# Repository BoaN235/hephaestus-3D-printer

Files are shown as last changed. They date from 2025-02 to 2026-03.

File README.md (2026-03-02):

# Hephaestus-1v2
title: "Hephaestus-1v2"
description: "A Core XY Printer with a z axis tilt"
Made by : Boa_N

Total Time: 7 hours

## Goals and Requirments
- Idk if i wanna do 235x235 or 220x220
- CoreXY
- Encolsed
- Z Tilt bed
- Compressed into a small footprint ~360x360x470 mm or ~14.17x14.17x18.5 in
- I would like to design a pcb for this project

## info
  This version was built with the old parts of Hephaestus-1 an broken Ender 3V3 and a few new parts

## log
- ### Feb 21st - Feb 24th Toolhead Work Time: 2.5 hours
  
  

- ### Feb 25th - Mar 1st Main Body Overall Design Time 3.5 hours
  

# ------------------| OLD VERSION |------------------

# Hephaestus-1
title: "Hephaestus-1"
description: "A Core XY Printer"
Made by : Boa_N

Total time: 145 hours 50 mins (Idk how accurate this is probably pretty close tho)

- [x] I have a 3D printer or will be getting one before March 21st (friend)
  
Hephaestus is the god of artisens and craftsman. with this printer I want to be able to create cool things just like a artisen or craftsman would.

Nicknamed "fire hazard"

hpdrawingpng

## Goals and Requirments
- standard 235 x 235mm
- CoreXY
- Enclosed
- at least 150mm/s
- Klipper
- Open-Source
- won't burn my house down (I hope)
- Rigid for good printing qualtiy
- A Cool Logo Embossed somewhere
- RGB lights

## Helpfull Resources
- www.matterhackers.com/articles/anatomy-of-a-3d-printer

## BOM (Bill Of Materials)
| Name | Price | Amount | Total Price | Link | Quanity | Notes |
|---|---|---|---|---|---|---|
| Sherpa Extruder | 36.89 | 1 | 36.89 | [link](https://www.amazon.com/Accessories-Lightweight-Extruder-Compatible-Ender3v2/dp/B0CNPG9QB2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) | 1 | |
| E3D V6 | 13.5  | 1 | 13.5 | [link](https://www.amazon.com/Wangdd22-1-75mm-Printer-Extruder-Accessories/dp/B06XBXDJY3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) | 1 | |
| mini fan 2-pack | 10.99 | 1 | 10.99 | [link](https://www.amazon.com/MakerFocus-Printer-40X40X10mm-Appliances-Replacement/dp/B07CH6YC32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) | 2 | |
| linear rail guide 2pc | 35.99 | 1 | 35.99 | [link](https://www.amazon.com/IMETRX-MGN12H-Printer-Machine-Upgrade/dp/B09ZPHPB5F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) | 2 | |
| Timing Belt 5M & pullys | 16.99 | 1 | 16.99 | [link](https://www.amazon.com/Zeelo-Timing-Tensioner-Torsion-Printer/dp/B08SMFM3Z6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) | 7 | |
| Al Exstrusion 2020 400mm 8pc | 26.99 | 1 | 26.99 | [link](https://www.amazon.com/Aluminum-Extrusion-European-Standard-Anodized/dp/B0CLGZ614N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) | 8 | |
| SKR Mini BigTree V3 | 39.99 | 1 | 39.99 | [link](https://www.microcenter.com/product/645749/bigtreetech-upgrade-skr-mini-e3-v30-control-board-32bit-for-ender-3-motherboard-silent-board-with-tmc2209-uart-stepper-dri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) | 1 | |
| Nema Stepper Moter 3PC | 16.1  | 1 | 16.1 | [link](https://www.amazon.com/BESJMYT-Stepper-39-65oz-1-3A-2-86V-1-66x1-66x1-5inch/dp/B0D22DR6P5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) | 3 | |
| Hot Bed | 18.59 | 1 | 18.59 | [link](https://www.amazon.com/Aluminum-Heated-Upgrade-Printer-220x220mm/dp/B09QWBSD3B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) | 1 | |
| BedScrews | 11.69 | 1 | 11.69 | [link](https://www.amazon.com/TIOPY-Printer-Leveling-Upgrade-Silicone/dp/B0BRCXX769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) | 0 | |
| EndStops | 8.99  | 1 | 8.99 | [link](https://www.amazon.com/ALMOCN-Mechanical-Endstop-Switch-Printer/dp/B08L5W4WM5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) | 6 | |
| Lead Screw | 9.99  | 1 | 9.99 | [link](https://www.amazon.com/ReliaBot-400mm-Thread-Starts-Printer/dp/B078R2XLXW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) | 1 | |
| Power Supply | 20.66 | 1 | 20.66 | [link](https://www.amazon.com/SUPERNIGHT-Switching-Universal-Regulated-Transformer/dp/B01LATMSGS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) | 1 | |
| Rasbery Pi | 24.99 | 0 | 0 | [link](https://www.microcenter.com/product/514076/raspberry-pi-3-model-a-board) | 1 | |
| PTFE Tubes | 8.99  | 1 | 8.99 | [link](https://www.amazon.com/Ultra-Smooth-Teflon-Tubing-Friction-Creality/dp/B0DLV5C1JS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) | 1 | |
| 1 Stepper moter | 6.99  | 1 | 6.99 | [link](https://www.amazon.com/Nema17-Stepper-Motor-Bipolar-4-Lead/dp/B09SV33XS2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) | 1 | |
| M3-Screws | 9.99  | 1 | 9.99 | [link](https://www.amazon.com/800Pcs-Socket-Assortment-Washers-Printing/dp/B0DR92YVL5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) | 800 | |
| M5-Screws | 9.99  | 1 | 9.99 | [link](https://www.amazon.com/Bemaka-200PCS-Button-Washers-Assortment/dp/B0CSY7FMQD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) | 200 | |
| M3-M5 heated Inserts | 15.98 | 1 | 15.98 | [link](https://www.amazon.com/Ktehloy-Threaded-Assortment-Printing-Components/dp/B0CLKDPN65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) | 420 | |
| Linear Motion Rods 4pc 400mm | 16.99 | 1 | 16.99 | [link](https://www.amazon.com/8mm-300mm-Vigorous-Hardened-Printer/dp/B0CXTX5FZ3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) | 2 | |
| Build Surface | 0 | 1 | 0 | [link](https://www.amazon.com/HICTOP-Heated-Bed-Printers-235mm/dp/B09TPFTM4Z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) | 1 | |
| Logitech quickcam 9000 | 10.99 | 0 | 0 | N/A (its too old) | 1 | |
| Linear Bearing | 8.99  | 1 | 8.99 | [link](https://www.amazon.com/uxcell-LMF8UU-Bearings-Machine-Printer/dp/B0DS8V2J7Y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) | 2 | I know it is old but its what I have |
| Plywood | 21.23 | 0 | 0 | [link](https://www.homedepot.com/p/Handprint-1-2-in-x-2-ft-x-4-ft-BCX-Sanded-Plywood-Actual-0-451-in-x-23-75-in-x-47-75-in-300896/202093833) | 1 | |
| SprayPaint | 5.98  | 0 | 0 | [link](https://www.homedepot.com/p/Rust-Oleum-Painter-s-Touch-2X-12-oz-Gloss-Black-General-Purpose-Spray-Paint-334026/307244831) | 1 | |
| PCB | 10 | 0 | 0 | N/A (I made it) | 1 | |
| Lights | 13.99 | 1 | 13.99 | [link](https://www.amazon.com/SEZO-Individually-Addressable-Programmable-Non-Waterproof/dp/B097BWJGYK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) | 1 | |
| Needed | | | 359.27 | | | |
| Total | | | 432.46 | | 1467 | |

# Log

## Research and Initial Design
Day 1 - 3

Feb 15 - Feb 17 2025

3 hour 20 min

Over the first three days, I conducted extensive research on 3D printer fundamentals and began planning the project. With very limited experience in 3D printing and no current access to a printer, I focused on understanding core design principles. I decided on using a CoreXY system and developed a project logo while outlining the initial design plan. To simplify the build and enhance manageability, I established some base requirements and identified components that would make construction easier. After evaluating different control boards, I settled on the SKR E3 V3 Mini, running Klipper on a Raspberry Pi 5, which I already had on hand.

## CAD Design
Day 4 - 16

Feb 18 - Mar 2 2025

55 hours 30 min

This was a long process, as I had never designed such a complicated system before. I used Fusion 360 for the design. Initially, I started with the frame using 4040 extrusions but later switched to 2020 extrusions to reduce costs. I designed the print head and Z-axis last, as they were among the most complex parts. The print head, in particular, was challenging because it required multiple intricate components to fit together precisely. Throughout the process, I faced many challenges—most of the parts I initially selected were the wrong size or too expensive, forcing me to refine the model multiple times. Despite these difficulties, this project taught me a lot about designing complex systems.
1. I started by working on the frame. I started the frame using 4040 extsrusion until I relized its like a 40 dollar diffrince if I use 2020 extrusions which I found way later. 10 hours



2. I worked on mounting the moters. I chose to put the moters on top of the extrusions for a "cleaner" look. turns out this makes the entire printer much harder to design. This includes the carriage and belt system. This took around 12 hours 



3. I created the printer head which took way longer than I want to admit to start. I have never designed something like this before which was a major challange. It is very hard to design around multiple diffrint parts and get them to fit all together however I did get it to work. This took around 12 hours. 



4. I added the z-axis moter and the base plate. The printer will have around a 250x250 build area. I had a hard time creating a part that would support the plate in all the places it needed to. This part was not that hard to create. 5.5 hours 



5. I worked on adding some cosmetic feauters to give my printer a clean look. I also added some areas to allow for airflow to go over the electronics inside. I added that can hold lights that will be added later and connected to the rasbery pie. I also added a box around the pcb and base for a cleaner astetch. 4 hours 



6. At the end I just did some genral work to make evreything cleaner and work better this took the rest of the time on the cad design. 12 hours


## BOM
Day 17 - 23

Mar 3 - Mar 15 2025

15 hours

Day 17 to 23, I compiled a detailed Bill of Materials (BOM), focusing on cost-effective sourcing strategies. To reduce expenses, I opted to 3D print some parts while using plywood for others due to its strength compared to printed components and its affordability relative to metal alternatives. Most of the required parts were sourced from Amazon to take advantage of cheap shipping and fast delivery. The process of finding affordable yet high-quality components took considerable time, but it ensured that the build would be both efficient and budget-friendly.

[BOM](https://1drv.ms/x/s!AtB5HagkhaZKhNYfKxltnQ1aC1ww8Q?e=Vdj45F)

## PCB

Day 24 - 25

Mar 16 - Mar 17 2025

4 hours

On day 24, I designed a custom PCB to serve as a control panel mounted on the front of the printer. This board features an OLED screen for displaying information, four integrated buttons housed within a shell, and connection pads for linking it to the Raspberry Pi. The PCB design enhances the user interface and accessibility of the printer, ensuring a smoother operation experience.




## assembly  

Assembly happend in 3 stages
  1. building the base - 10 hours 
  2. reprinting evreyting 20 times - 24 hours 150+ hours printing
  3. getting the thing to move **correctly** - 6 hours

### building the base/frame
  When I was building the frame I put it onto the wood however the wood started to warp becuase I did a bad job cutting it with a jigsaw so I eventualy had to remove that part as it warped. The frame however worked well and was pretty easy to put together after I cut the alumuinum extrusions. there is a slight problem about not being level but I can put a small messed up print and it fixes it

### Printed Parts/Smaller Mechanisms
  This step took up the most time as I had to spend days upon days reprinting parts. I eventualy got up to around 250 hours on my printer. most parts wouldn't work in the first try so I would reprint it then try again. A huge amount of the parts I bought did not imedieatly work so I had to change my design and reprint a ton of parts.

### software and movment
  The software was the eseiast part to build. I used the klipper firmware with some smaller changes to allow the printer to work. Seeing the printer come to life and first move was my favoruite part. I was so exicted to see my design working it didn't take much longer to get the printer to print. However it started to skip and after a lot of tightning parts it worked well I got a very good looking benchy that compares to the kobra 3 I used to print parts.












































# Final Designs

### CAD



### BOM

[BOM](https://1drv.ms/x/s!AtB5HagkhaZKhNYfKxltnQ1aC1ww8Q?e=Vdj45F)### PCB



## Extra Images
-   HephaestusLogo
-   
-   
-   
-   
-   
-   
-   
-   
-   
-   
-   
-   
-   
-   
-   
-   
-   
-   
-   
-   
-   
-   
-   
-   
-   
-   
-   

### Extrusion Lenghts
5x 320 mm 32 cm 12.5984 inchs
2x 100 mm 10 cm 3.93701 inchs
2x 440 mm 44 cm 17.3228 inchs
2x 490 mm 49 cm 19.2913 inchs

### Printed parts 
2x side pecies
2x head rail holders
1x front head

1x back head
2x moter mounts
4x top holders
2x rail covers

the diffrince is like 80mm

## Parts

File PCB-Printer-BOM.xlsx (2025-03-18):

Comment | Designator | Footprint
Adafruit_SSD1306 | Display | SMD
Button_Switch_THT:SW_PUSH_6mm | Button1, Button2, Button3, Button4 | THT

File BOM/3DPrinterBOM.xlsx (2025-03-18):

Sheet: Money
Name | Price | Amount | Total Price | Link | Quanity | Notes
Sherpa Extruder | 36.89 | 1 | 36.89 | https://www.amazon.com/Accessories-Lightweight-Extruder-Compatible-Ender3v2/dp/B0CNPG9QB2 | 1
E3D V6 | 13.5 | 1 | 13.5 | https://www.amazon.com/Wangdd22-1-75mm-Printer-Extruder-Accessories/dp/B06XBXDJY3 | 1
mini fan 2-pack | 10.99 | 1 | 10.99 | https://www.amazon.com/MakerFocus-Printer-40X40X10mm-Appliances-Replacement/dp/B07CH6YC32 | 2
linear rail guide 2pc | 35.99 | 1 | 35.99 | https://www.amazon.com/IMETRX-MGN12H-Printer-Machine-Upgrade/dp/B09ZPHPB5F?s=industrial | 2
Timing Belt 5M & pullys | 16.99 | 1 | 16.99 | https://www.amazon.com/Zeelo-Timing-Tensioner-Torsion-Printer/dp/B08SMFM3Z6?s=industrial | 7
Al Exstrusion 2020 400mm 8pc | 26.99 | 1 | 26.99 | https://www.amazon.com/Aluminum-Extrusion-European-Standard-Anodized/dp/B0CLGZ614N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 | 8
SKR Mini BigTree V3 | 39.99 | 1 | 39.99 | https://www.microcenter.com/product/645749/bigtreetech-upgrade-skr-mini-e3-v30-control-board-32bit-for-ender-3-motherboard-silent-board-with-tmc2209-uart-step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 | 1
Nema Stepper Moter 3PC | 16.1 | 1 | 16.1 | https://www.amazon.com/BESJMYT-Stepper-39-65oz-1-3A-2-86V-1-66x1-66x1-5inch/dp/B0D22DR6P5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 | 3
Hot Bed | 18.59 | 1 | 18.59 | https://www.amazon.com/Aluminum-Heated-Upgrade-Printer-220x220mm/dp/B09QWBSD3B | 1
BedScrews | 11.69 | 1 | 11.69 | https://www.amazon.com/TIOPY-Printer-Leveling-Upgrade-Silicone/dp/B0BRCXX769 | 0
EndStops | 8.99 | 1 | 8.99 | https://www.amazon.com/ALMOCN-Mechanical-Endstop-Switch-Printer/dp/B08L5W4WM5 | 6
Lead Screw | 9.99 | 1 | 9.99 | https://www.amazon.com/ReliaBot-400mm-Thread-Starts-Printer/dp/B078R2XLXW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 | 1
Power Supply | 20.66 | 1 | 20.66 | https://www.amazon.com/SUPERNIGHT-Switching-Universal-Regulated-Transformer/dp/B01LATMSGS | 1
Rasbery Pi | 24.99 | 0 | 0 | https://www.microcenter.com/product/514076/raspberry-pi-3-model-a-board | 1
PTFE Tubes | 8.99 | 1 | 8.99 | https://www.amazon.com/Ultra-Smooth-Teflon-Tubing-Friction-Creality/dp/B0DLV5C1JS?cv_ct_cx=ptfe%2Btubes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 | 1
1 Stepper moter | 6.99 | 1 | 6.99 | https://www.amazon.com/Nema17-Stepper-Motor-Bipolar-4-Lead/dp/B09SV33XS2?mcid=b2142c4ff14734c08300cc536244800b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 | 1
M3-Screws | 9.99 | 1 | 9.99 | https://www.amazon.com/800Pcs-Socket-Assortment-Washers-Printing/dp/B0DR92YVL5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 | 800
M5-Screws | 9.99 | 1 | 9.99 | https://www.amazon.com/Bemaka-200PCS-Button-Washers-Assortment/dp/B0CSY7FMQD?s=industrial | 200
M3-M5 heated Inserts | 15.98 | 1 | 15.98 | https://www.amazon.com/Ktehloy-Threaded-Assortment-Printing-Components/dp/B0CLKDPN65 | 420
Linear Motion Rods 4pc 400mm | 16.99 | 1 | 16.99 | https://www.amazon.com/8mm-300mm-Vigorous-Hardened-Printer/dp/B0CXTX5FZ3?s=industrial | 2
Build Surface | 0 | 1 | 0 | https://www.amazon.com/HICTOP-Heated-Bed-Printers-235mm/dp/B09TPFTM4Z | 1
Logitech quickcam 9000 | 10.99 | 0 | 0 | N/A (its too old) | 1
Linear Bearing | 8.99 | 1 | 8.99 | https://www.amazon.com/uxcell-LMF8UU-Bearings-Machine-Printer/dp/B0DS8V2J7Y?s=industrial | 2 | I know it is old but its what I have
Plywood | 21.23 | 0 | 0 | https://www.homedepot.com/p/Handprint-1-2-in-x-2-ft-x-4-ft-BCX-Sanded-Plywood-Actual-0-451-in-x-23-75-in-x-47-75-in-300896/202093833 | 1
SprayPaint | 5.98 | 0 | 0 | https://www.homedepot.com/p/Rust-Oleum-Painter-s-Touch-2X-12-oz-Gloss-Black-General-Purpose-Spray-Paint-334026/307244831 | 1
PCB | 10 | 0 | 0 | N/A (I made it) | 1
Lights | 13.99 | 1 | 13.99 | https://www.amazon.com/SEZO-Individually-Addressable-Programmable-Non-Waterproof/dp/B097BWJGYK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 | 1
Needed |  |  | 359.27
Total |  |  | 432.46 |  | 1467

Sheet: Screws
Size | Nut | HeatedInset
M3x8F | No | No
M3x10F | Yes | Yes
M5x45 | Yes | yes
M3x30F | Yes | Yes

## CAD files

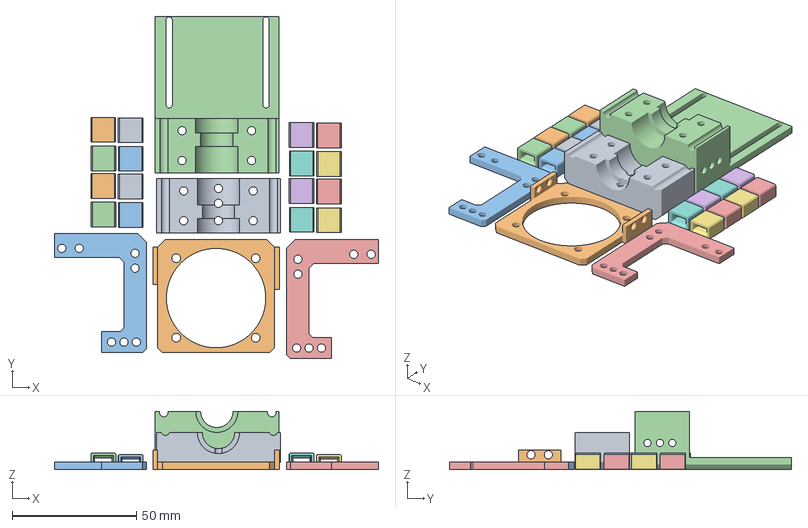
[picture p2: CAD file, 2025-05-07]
2x-belt-holder-thin-gt2.3mf
130.6 x 137.7 x 23.5 mm
x-belt-holder-thin-gt2.stl x 8
x-belt-holder-gt2.stl x 8
V5FrontHotend.stl
V2Fan.stl
V2HolderFan.stl x 2
V5BackHotend.stl

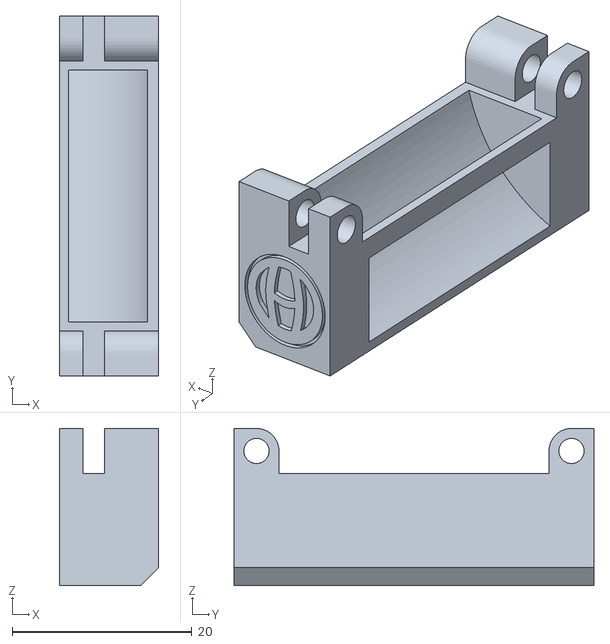
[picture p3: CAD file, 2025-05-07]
DesignFiles/Parts/PrintHead/V1Cooler.stl
11.0 x 40.0 x 17.5

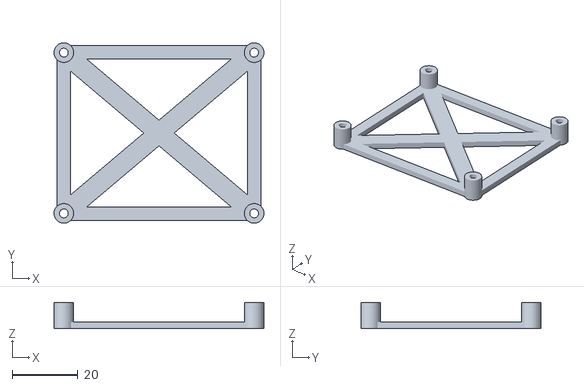
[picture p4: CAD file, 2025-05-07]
DesignFiles/Parts/V1RPI4Holder.stl
64.0 x 55.0 x 8.00

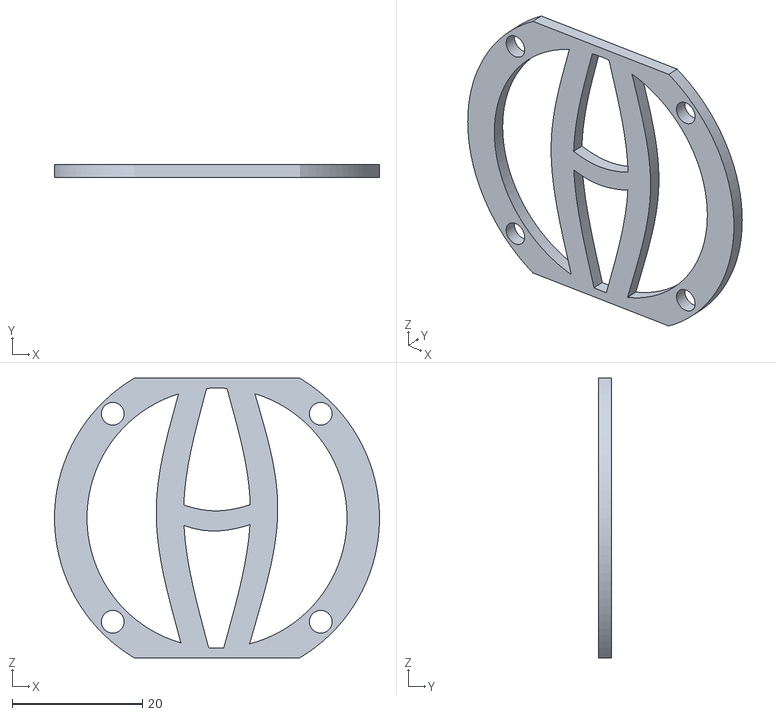
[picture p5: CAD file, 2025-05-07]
DesignFiles/Parts/PrintHead/V1logofront.stl
50.0 x 2.00 x 43.0

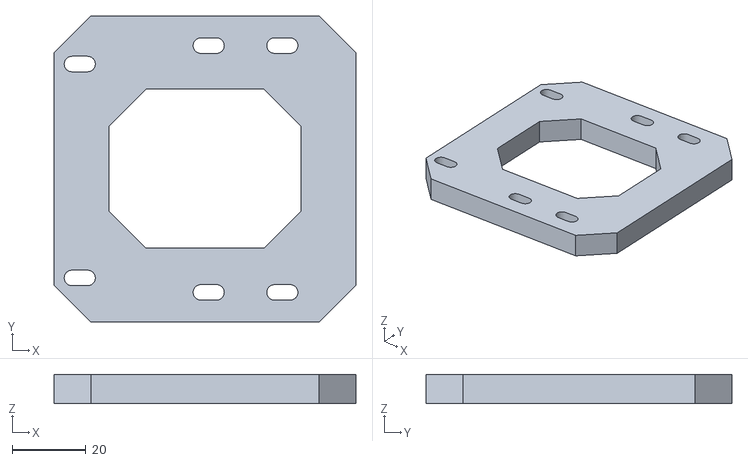
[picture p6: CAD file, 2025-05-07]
DesignFiles/Parts/V2CarridgeBridge.stl
82.0 x 83.0 x 8.00

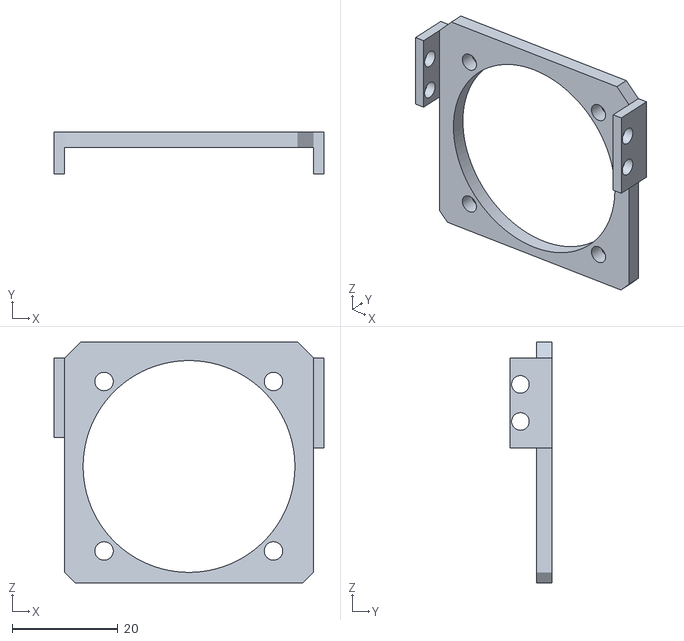
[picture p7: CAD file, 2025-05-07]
DesignFiles/Parts/PrintHead/V2Fan.stl
51.0 x 8.00 x 45.5

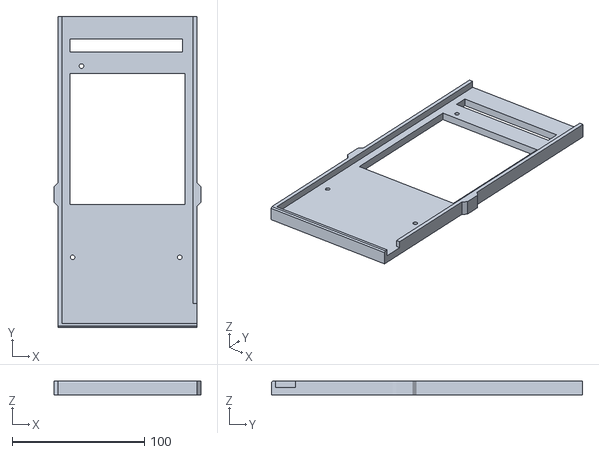
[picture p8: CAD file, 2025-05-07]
DesignFiles/Parts/V3Powersupplybottom.stl
111.0 x 235.0 x 10.5

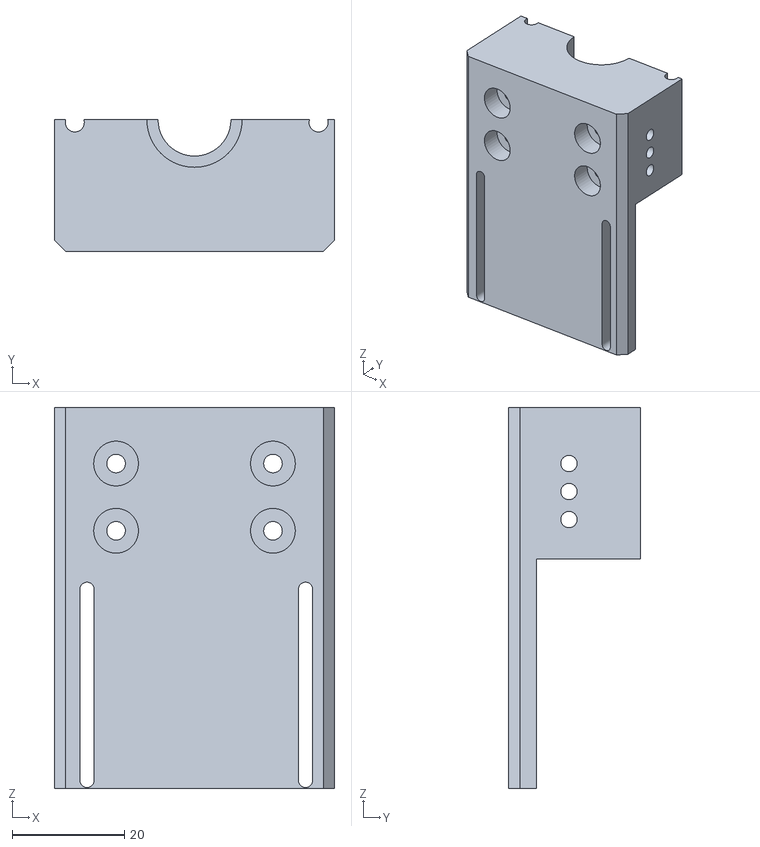
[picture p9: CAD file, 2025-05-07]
DesignFiles/Parts/PrintHead/V6BackPrintHead.stl
50.0 x 23.5 x 68.0

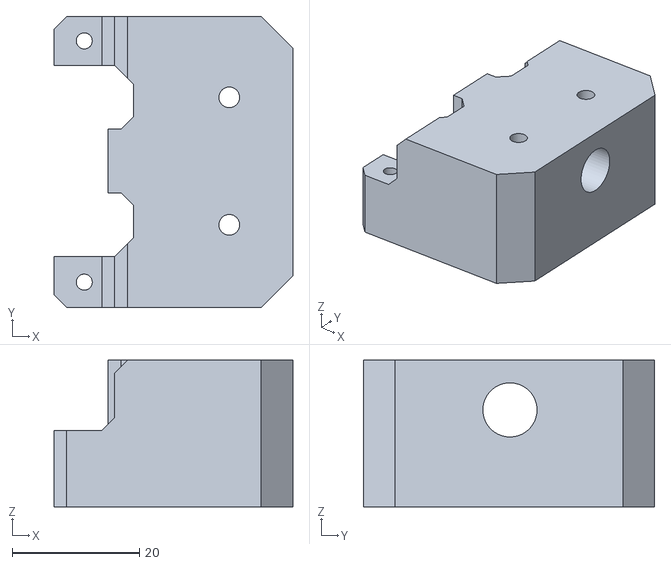
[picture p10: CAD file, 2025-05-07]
DesignFiles/Parts/V10GantryTop.stl
37.5 x 45.7 x 23.0

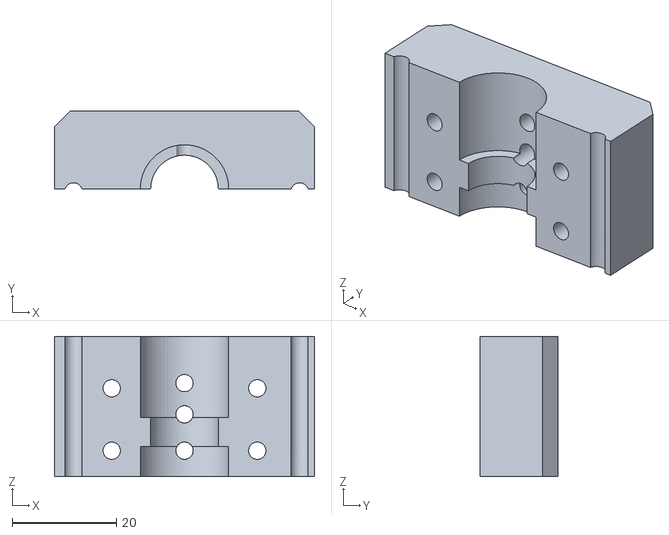
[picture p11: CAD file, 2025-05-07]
DesignFiles/Parts/PrintHead/V6FrontPrintHead.stl
50.0 x 15.0 x 27.0

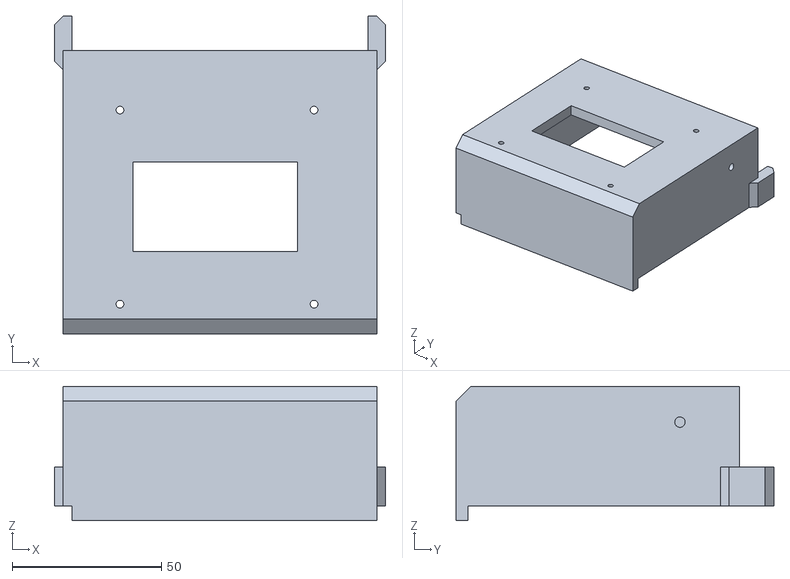
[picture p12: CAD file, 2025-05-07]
DesignFiles/Parts/V2PowerSupplyholder.stl
111.0 x 106.5 x 45.0

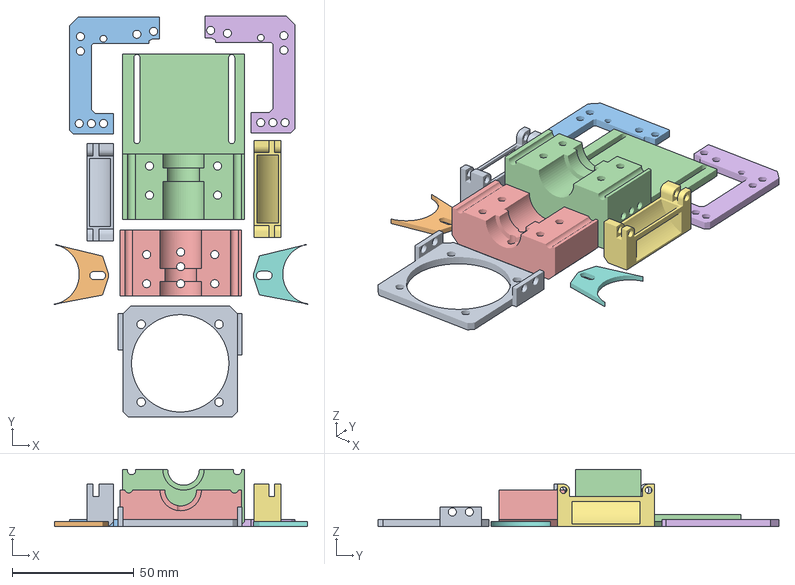
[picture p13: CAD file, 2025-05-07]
DesignFiles/Parts/PrintHead/HeadPrint.3mf
104.0 x 164.7 x 23.5 mm
V1Cooler.stl x 2
V1Idkatthispoint.stl x 2
V5Arm.stl x 2
V6BackPrintHead.stl
V6FrontPrintHead.stl
V2Fan.stl

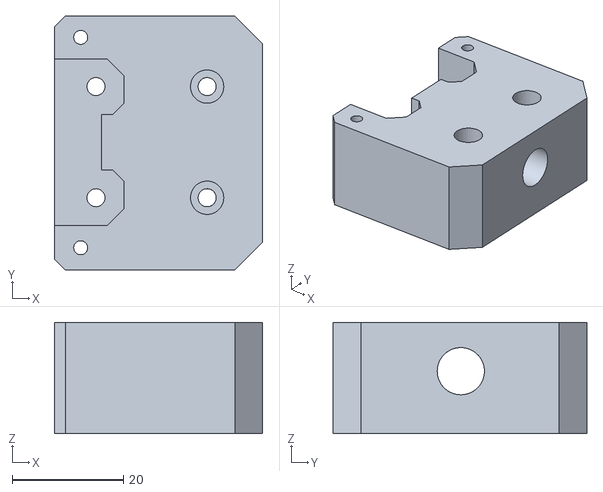
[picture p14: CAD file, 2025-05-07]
DesignFiles/Parts/V10GantryBottom.stl
37.5 x 45.7 x 20.0

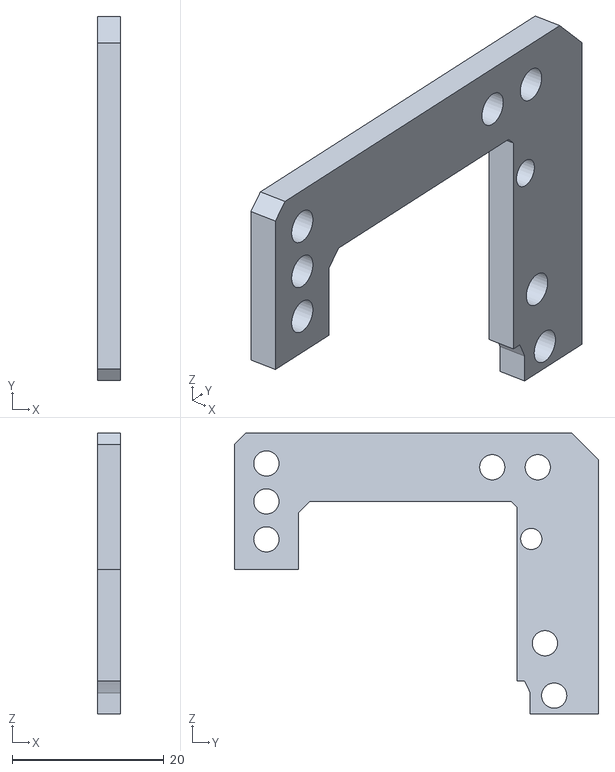
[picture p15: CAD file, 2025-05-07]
DesignFiles/Parts/PrintHead/V5Arm.stl
3.00 x 48.0 x 37.0

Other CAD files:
DesignFiles/Parts/V2BottomPowerSupply.stl
DesignFiles/Parts/PrintHead/V1Idkatthispoint.stl
DesignFiles/Parts/V3BedCarrige.stl
DesignFiles/Parts/Back v2.stl
DesignFiles/Parts/BottomV4.stl
DesignFiles/Parts/V1SkrMiniHolder.stl
DesignFiles/Parts/V4Carrige.stl

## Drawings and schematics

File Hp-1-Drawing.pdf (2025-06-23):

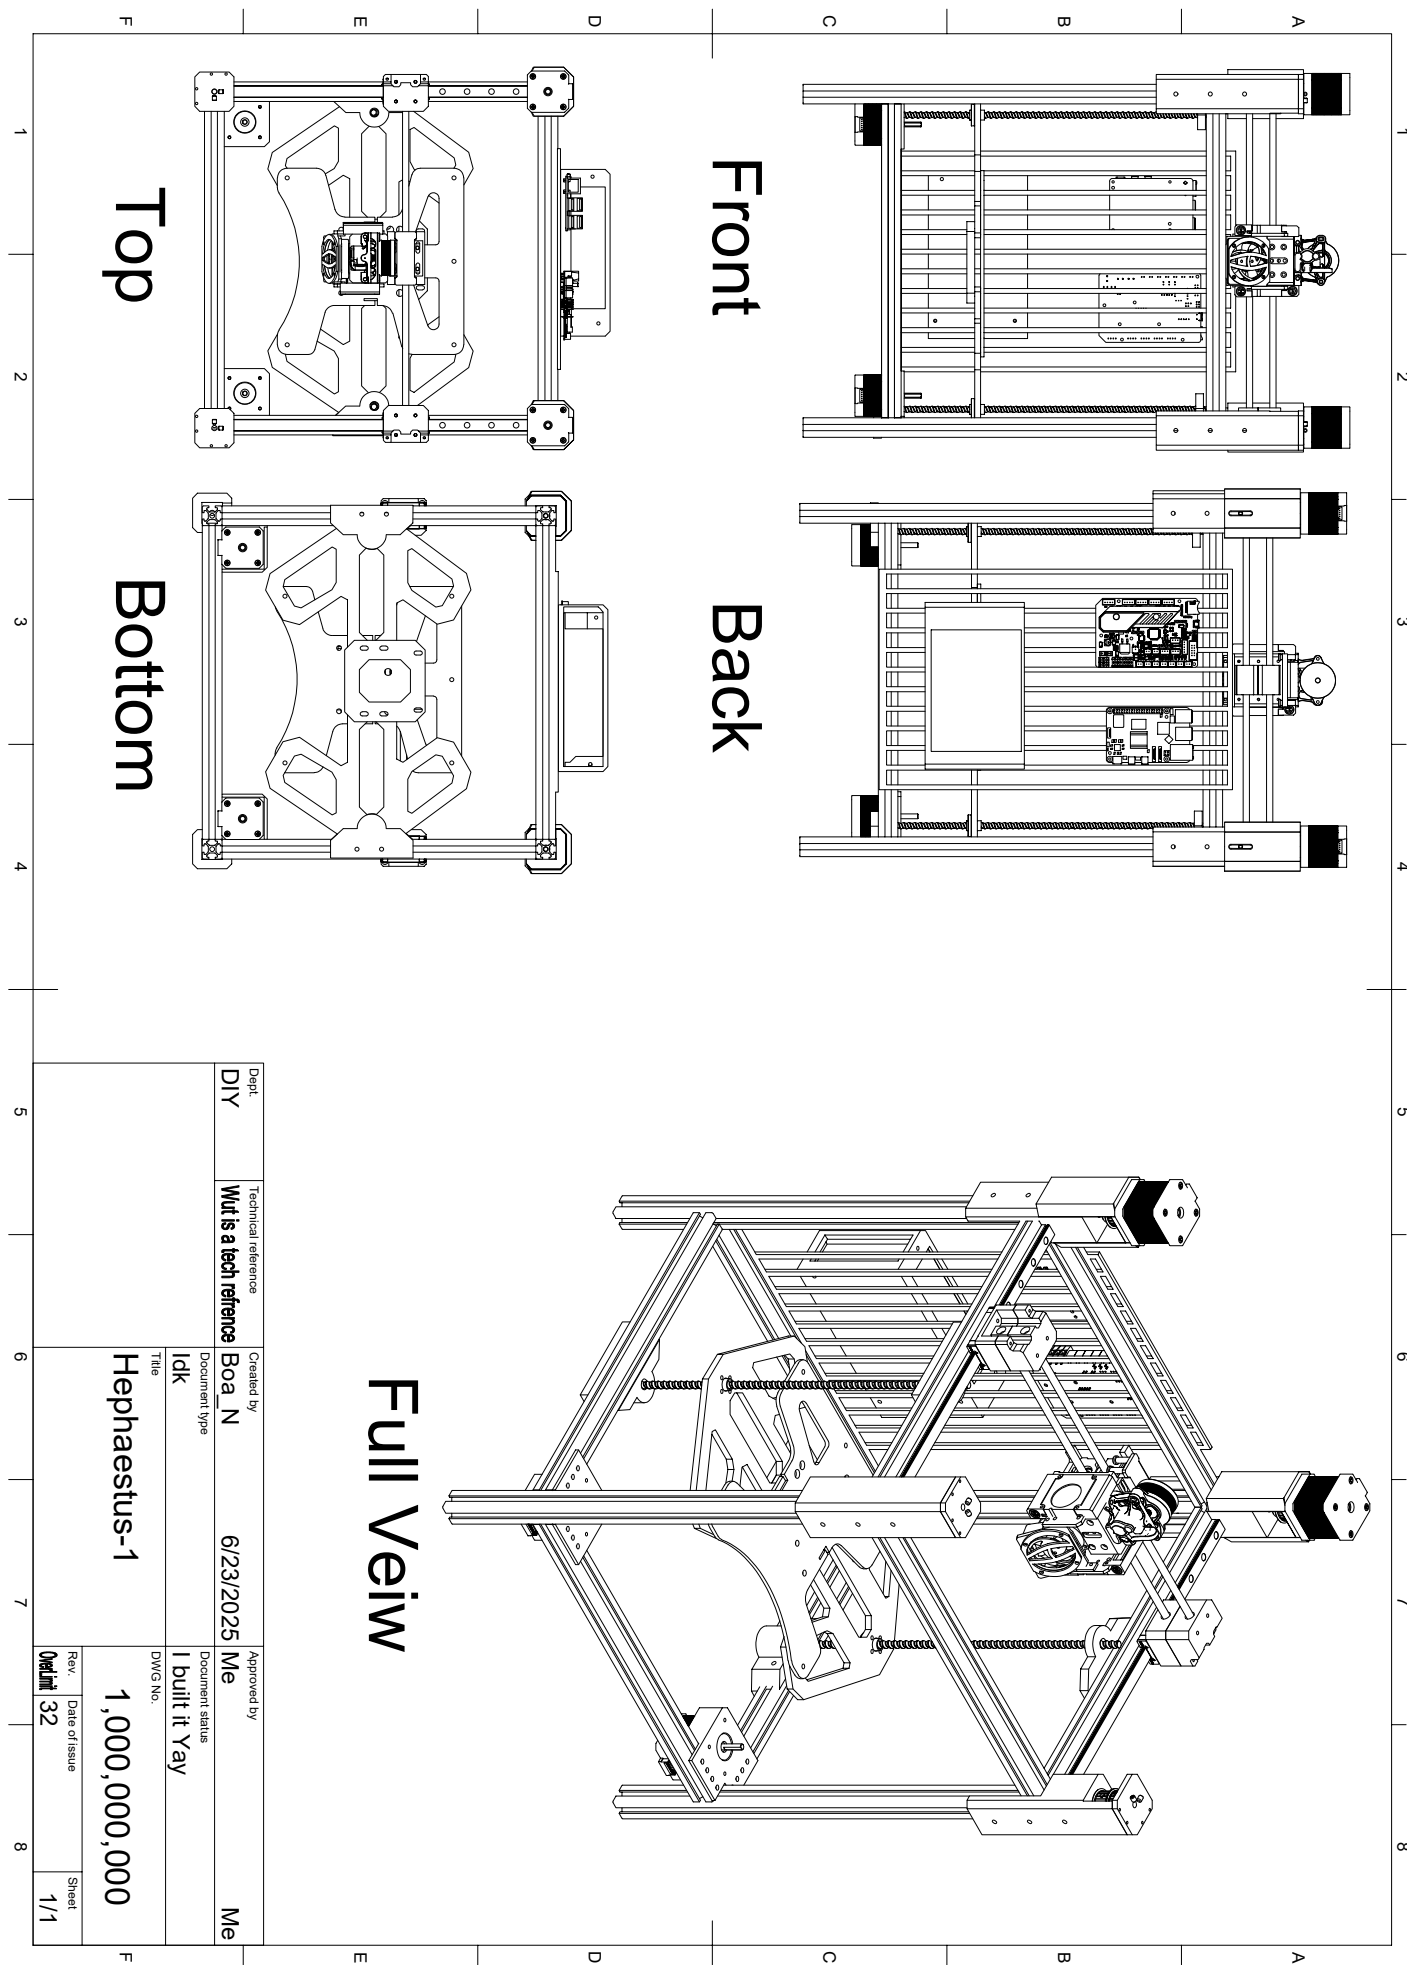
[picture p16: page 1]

1 A 2 3 4 5 6 7 8 1 2 3 4 5 6 7 8 FEDCB FEDCBA Dept. Technical reference Created by Approved by Title DWG No. Document type Document status Rev. Date of issue Sheet 32 I built it Yay Idk Me 6/23/2025 1/1 1,000,000,000 Hephaestus-1 Me Boa_N DIY

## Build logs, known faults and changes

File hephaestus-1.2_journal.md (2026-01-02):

# Hephaestus-1.2
title: "Hephaestus-1.2" 

Made by : Boa_N

Total time: 2 hours

## Redesing Goals
- 235 x 235mm bed size
- Redo Frame
- Fix Head (Make it smaller)
- Make it a more Stable Bed
- Enclosed
- RGB lights

### older version Hephaestus-1.1


---

## Day 1 
I started the redesign before I created this log.

I am planing on getting new linear exstrusians because the ones I cut were off and I don't have enough space to fit into.



total time: 2 hours

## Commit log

2025-03-15 added stl zip file
2025-03-18 Remove obsolete design files and logo assets
    [3DPrinterBOM.xlsx]
2025-05-07 adding some files
    [Back v2.stl, BottomV4.stl, HeadPrint.3mf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]
